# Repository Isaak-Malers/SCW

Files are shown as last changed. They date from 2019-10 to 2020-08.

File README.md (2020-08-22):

# Shaft Collar Weapon:

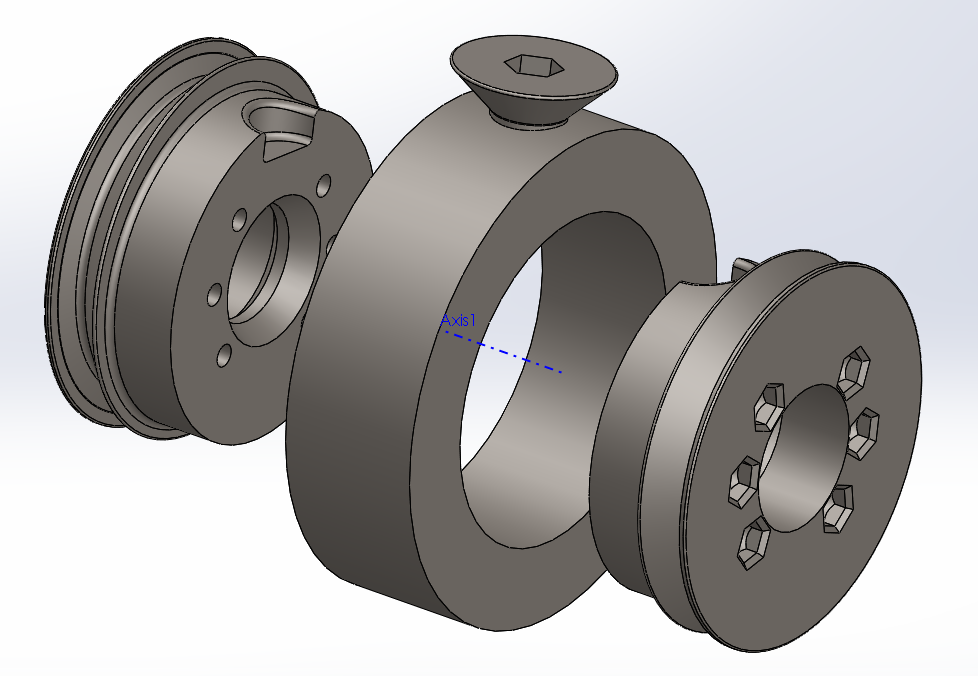
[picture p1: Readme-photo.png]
Exploded View


Video of weapon in action:  https://www.youtube.com/watch?v=2M8aIPILqEA

# Parts Required for Included design:
* 3d printed hubs in the requisite size
* 40mm length M3 countersunk bolts
* M3 Nylock nuts
* 608 "Skateboard" ball bearings
* Requisite size steel shaft collar
* Requisite size countersunk bolt, Length should be the shortest size that still sits proud of the inner race of the shaft collar.
* 1/8 diameter O-Ring, sized so that it stretches around 30% when stretched onto both pulleys.

# Integration Requirements:
* Weapon motor/pulley, I've included STL's for the pulley I use.  Which mates to a GARTT 2212 920kv motor with the plain can (no integrated prop addapter)
* 8mm weapon shaft/spacers/mounting

# Design Recomendations:
* The 2 inch shaft collar + hub weighs just shy of 20oz.
* The 1.875 shaft collar + hub weighs just shy of 17oz.
* I typically buy collars in 4 packs on ebay.  The 2 inch collar is a very common size and my per-unit cost is typically around 4$
* The motor I reccomend with the included pulley STL's is capable of starting from stall with the robot sitting with 100% of its weight on the weapon (at 4s, 30a esc)
* I reccomend spinning the weapon around 2,500-7,000 rpm, Faster speeds typically throw O-rings, and because the mass/moment of the weapon is so optimized, it really doesn't need crazy RPM's to do damage.
* Note that the hub includes 2 pulleys for 2 O-rings.  For higher tip speeds, I've used dual 2212 1400kv motors to increase the power to the weapon.
* The weapon hub can generally be printed from any type of plastic and it will usually hold up fine without breaking.  The bigger problem is heat.  PLA hubs will melt in a long match as the Oring friction builds up.

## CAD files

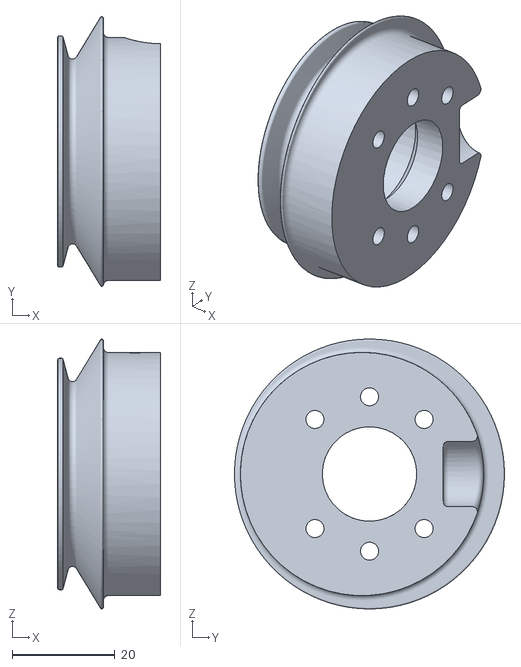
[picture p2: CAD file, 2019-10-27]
collar_1_875_inch/nuts.STL
19.9 x 52.5 x 52.5

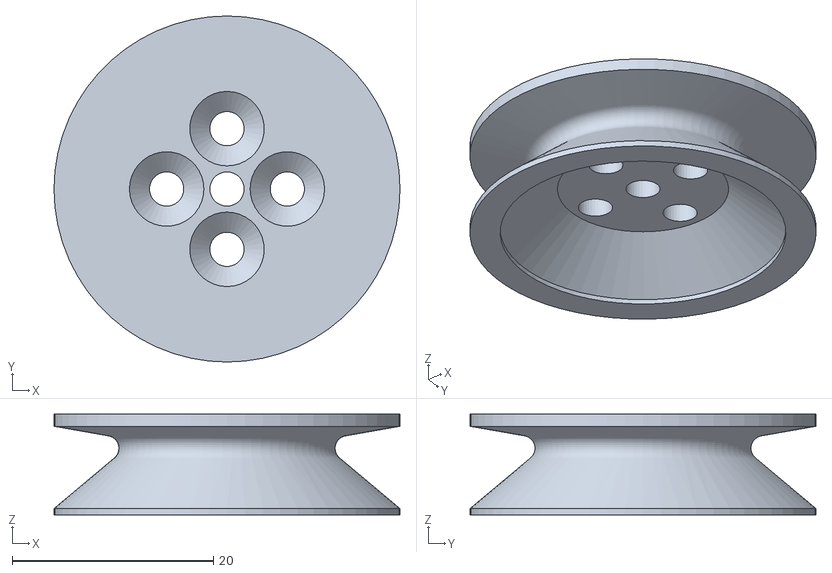
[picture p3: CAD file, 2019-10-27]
motor_gart_2212/GARTT-motor-pulley.STL
34.4 x 34.4 x 10.0

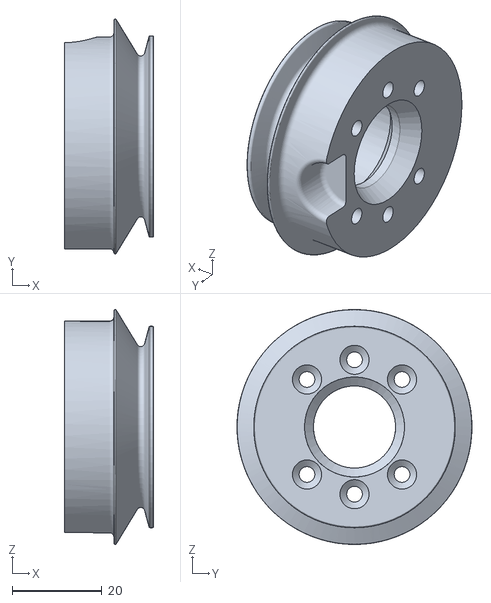
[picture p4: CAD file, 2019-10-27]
collar_1_875_inch/countersink.STL
20.0 x 52.5 x 52.5

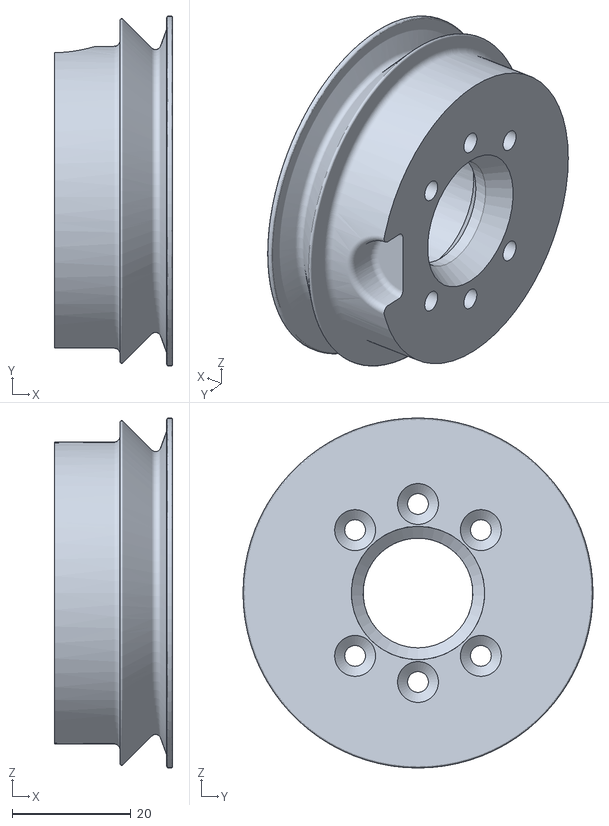
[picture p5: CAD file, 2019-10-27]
collar_2_inch/countersunk-side.STL
20.0 x 59.0 x 59.0

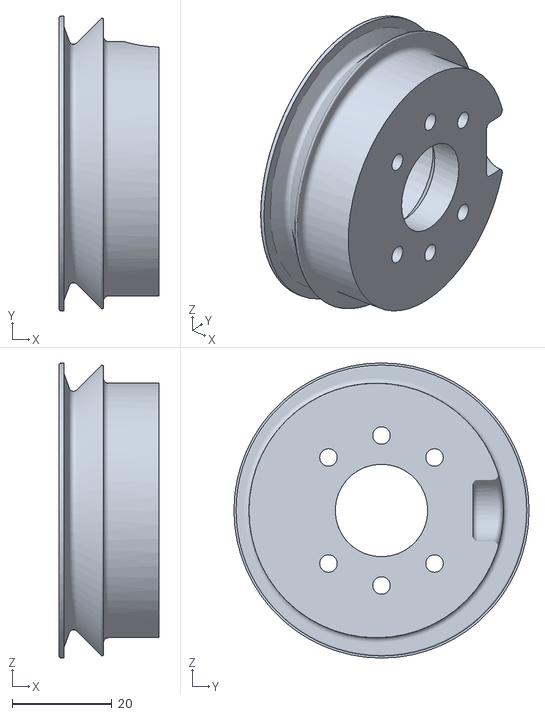
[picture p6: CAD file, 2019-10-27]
collar_2_inch/nut-side.STL
19.9 x 59.0 x 59.0
